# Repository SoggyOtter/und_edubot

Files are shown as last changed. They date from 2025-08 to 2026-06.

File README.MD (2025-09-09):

# UND_EDUBot Overview

[Build Instructions Playlist](https://www.youtube.com/playlist?list=PLYcNE-BB9RCs-w1YGQMMMpfctwIbQ31T8)

# Build the robot

The parts list for the is in the parts list excel file.  Purchase the needed components to build the robot.

If you are building the robot with others several people can build one robot with multi packs of screws and wire.

The CAD models for printing are found in the /build/CAD Models directory.  The .3mf files can be imported directly to the slicer of your choosing for printing.  It is reccommended to use support material, however, acceptable results can be achieved without supports.

Soldering and assembly of the electrical components should be done following the wiring diagram found in the wiring diagram power point in the /build directory

## Tools Needed:

- 3D printer
- Soldering iron & solder
- Metric hex key set
- Small flat head screwdriver
- Small pliers

# Build Instructions

Build instructions will be provided by youtube videos which will be posted.  Following the video instructions and diagrams provide all the information needed to build the robot.

# Powering up for the first time

Once the robot is built you can power up the pi with a flashed micro SD card.

In the /software/Pi Image directory the image for the raspberry pi is provided.  Download the .img file and use the Raspberry Pi Imager to flash the micro SD card with the image.

TODO add images

Select Pi 5 for the pi version

Click on operating system, scroll down and select use custom.  Then find the .img file you downloaded.

Click choose storage and select the micro SD card.  You will be prompted to set the host name and password, choose a name and password you will remember.

# UND Students Pi Image Files

Duplicate the SD card from https://ndusbpos-my.sharepoint.com/:u:/g/personal/john_merila_ndus_edu/EXtqe4LofwhBoTBZhCYkA34BFa9aUKt46IkEdTdlvLatog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 and follow the steps to flash a SD card

I am looking at alternative hosting or compression methods to allow for an image that can be hosted on github.

# Getting the robot running

<!--- The EDUBot uses ROS2 in a Docker container to manage the control of the robot.

Once the pi powers on open VS code, the easiest way is to open a terminal and run

```bash
code .
```

Once in vs code open the PiBot directory using file -> open folder -> PiBot

With the PiBot folder open use the hotkey ctrl+shift+p and type open in container.  This opens the docker container and allows you to control the robot.

BASIC STARTUP
Basic Startup:
 -->
1. 

open terminal and open VS code

```bash
code .
```

2.

file -> open folder

select pibot_repo

click on pop up Reopen in container

if no pop up ctrl-shift-p reopen in container

if it fails ctrl-shift-p rebuild and reopen container

3.

Follow readme located in ws/src/PiBot/Readme.txt

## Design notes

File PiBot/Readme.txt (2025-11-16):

To get RVIZ working
locally: xhost +local:docker

build work space
colcon build --symlink-install
*when first building the workspace it will take some time to build the lidar package
*it will fail on the first build, re run command and it will work

To source the local ROS workspace 
source install/setup.bash

Start up motor control and wheel encoders
ros2 launch PiBot PiBot_launch.py 

Start up lidar with visualization
ros2 launch sllidar_ros2 view_sllidar_a1_launch.py

For teleop control
ros2 run teleop_twist_keyboard teleop_twist_keyboard 

Topics for robot:

/

Notes:

If you are adding additional packages via sudo apt install . . . 

Put at the end of Dockerfile with run preceding
* add -y if it requires yes when installing

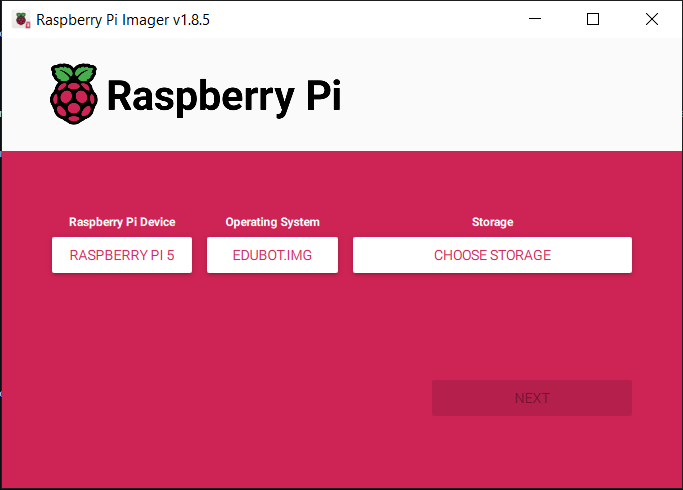
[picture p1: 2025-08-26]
docs/Photos/RPi Imager.PNG

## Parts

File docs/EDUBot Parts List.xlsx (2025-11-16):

Subsystem | Component | Number | Buy No. | Item Cost | Total Cost | Link
Drive | Motors | 2 | 2 | 12.99 | 25.98 | 163 RPM Mini Econ Gear Motor - ServoCity® (https://www.servocity.com/163-rpm-mini-econ-gear-motor/)
 | Wheels | 1 | 1 | 12 | 12 | Pololu Multi-Hub Wheel w/Inserts for 3mm and 4mm Shafts - 80×10mm, Black, 2-Pack (https://www.pololu.com/product/3690)
 | Ball Caster | 1 | 1 | 4.5 | 4.5 | Pololu Ball Caster with 3/4″ Metal Ball (https://www.pololu.com/product/955)
Electronics | Motor Controller | 1 | 1 | 12.99 | 12.99 | Pololu - TB67H420FTG Dual/Single Motor Driver Carrier (https://www.pololu.com/product/2999)
 | Encoders | 2 | 1 | 10 | 10 | Amazon.com: WWZMDiB 4Pcs AS5600 Magnetic Encoder 3.3V 12bit high Precision Magnetic Induction Angle Measurement Sensor Module，Mainly Used to Obtain Information Such as Progressive Motor Speed : Industrial & Scientific (https://www.amazon.com/WWZMDiB-Measurement-Module%EF%BC%8CMainly-Information-Progressive/dp/B0CM3C8KFT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)
 | Rpi | 1 | 1 | 80 | 80 | 2648-SC1112-ND
 | Rpi Active Cooler | 1 | 1 | 5 | 5 | 2648-SC1148-ND
 | Pi Camera | 1 | 1 | 25 | 25 | 2648-SC1223-ND
 | micro HDMI cable | 1 | 1 | 6.99 | 6.99 | Amazon.com: Amazon Basics Micro HDMI to HDMI Display Cable, 18Gbps High-Speed, 4K@60Hz, 2160p, 48-Bit Color, Ethernet Ready, 6 Foot, Black : Electronics (https://www.amazon.com/Amazon-Basics-Display-High-Speed-Ethernet/dp/B07KSDB25X?sp_csd=d2lkZ2V0TmFtZT1zcF9hdGY)
 | Gpio breakout | 1 | 1 | 10.99 | 10.99 | Amazon.com: Treedix RPi GPIO Terminal Block Breakout Board Module Expansion Board Compatible with Raspberry Pi 4B/3B+/3B/2B/Zero/Zero W : Electronics (https://www.amazon.com/Treedix-Terminal-Expansion-Compatible-Raspberry/dp/B09MFB6PJH)
 | Gpio standoff | 1 | 1 | 6.99 | 6.99 | Amazon.com: DSLRKIT 8.5mm GPIO and PoE Pin Header Height Increaser Extender for Raspberry Pi 5 4B 3B+ 3B (Pack of 2) : Electronics (https://www.amazon.com/DSLRKIT-8-5mm-Increaser-Extender-Raspberry/dp/B0F1F84GKV)
 | Lidar | 1 | 1 | 99 | 99 | 1738-1402-ND
 | 3S UPS | 1 | 1 | 32 | 32 | Amazon.com: Waveshare Uninterruptible Power Supply (UPS) Module, Supports Charging and Power Output at The Same Time, 3S & 5V 5A Output, Compatible with Raspberry Pi Board : Electronics (https://www.amazon.com/waveshare-Uninterruptible-UPS-Module-3S/dp/B0BQC2WNR8)
 | Micro USB cable | 1 | 1 | 6.99 | 6.99 | Amazon.com: Short Micro USB Cable 1ft [5 Pack] USB 2.0 Micro USB Charging Cable Android Charger Cord for Samsung Galaxy S7 Edge S6 J7 Note 5 LG Kindle Sony PS4 TV Stick Smartphones (Black) : Electronics (https://www.amazon.com/Android-Compatible-Smartphones-Charging-Stations/dp/B095JZSHXQ)
*6 for price of 3 | 18650 Battery | 3 | 1 | 20 | 20 | Amazon.com: Tokeyla 3.7 Volt 18650 Rechargeable Battery, 3000mAh Battery Flat Top Lithium Batteries for LED Flashlights, Headlamp (6 Pack) : Health & Household (https://www.amazon.com/Tokeyla-Rechargeable-Batteries-Flashlights-Headlamp/dp/B0DRCQHZRH)
 | Micro SD | 1 | 1 | 16.99 | 16.99 | Amazon.com: SanDisk 128GB Extreme microSDXC UHS-I Memory Card with Adapter - Up to 190MB/s, C10, U3, V30, 4K, 5K, A2, Micro SD Card - SDSQXAA-128G-GN6MA : Electronics (https://www.amazon.com/SanDisk-Extreme-microSDXC-Memory-Adapter/dp/B09X7BK27V)
Consumables Note* all of these are more than needed for one robot, if on campus multiple people can share parts | M4x8 | 4 | 1 | 24.98 | 24.98 | HELIFOUNER 1280 Pieces M2 M2.5 M3 M4 304 Stainless Steel Hex Socket Cap Metric Screws Bolts Washers Nuts Hardware Assortment Kit with Hex Wrenches: Amazon.com: Industrial & Scientific (https://www.amazon.com/HELIFOUNER-Stainless-Hardware-Assortment-Wrenches/dp/B09WJ14JWF)
 | M4x12 | 4 |  |  |  | This multi pack is the best way to get all you need for this robot and have extra for other projects
 | M2x8 | 8
 | M2x16 | 2 | Optional
 | M2 Nuts | 2 | Optional
 | M2.5x8 | 8
 | 24 gauge wire multi color |  | 1 | 15.99 | 15.99 | TUOFENG 24 AWG Flexible Silicone Wire, 30ft/9m Each (6 Colors), Tinned Copper Core, High Temp Resistant (-60C to +200C), Suitable for Electrical & Electronic Devices - Amazon.com (https://www.amazon.com/TUOFENG-Wire-Stranded-Flexible-Silicone-Different/dp/B07G2BWBX8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)
 | 20 gauge wire red/black |  | 1 | 10.98 | 10.98 | https://www.amazon.com/BNTECHGO-Silicone-Flexible-Strands-Stranded/dp/B07HGT7N29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
 | PLA Filament | 1
 | Small Zipties |  | 1 | 2.99 | 2.99 | Amazon.com: Zip Ties 4 inch, Small Zip Ties with 18 lb Tensile Strength, Black, 1000 Pack, by Tantti Supply : Electronics (https://www.amazon.com/Small-Tensile-Strength-Tantti-Supply/dp/B0C2KGK2HR?sp_csd=d2lkZ2V0TmFtZT1zcF9hdGY)
Optional Accessories | Small Router | 1 | 1 | 34 | 34 | Amazon.com: GL.iNet GL-AR300M16-Ext Portable Mini Travel Wireless Pocket Router - WiFi Router | OpenWrt | 2 x Ethernet Ports | OpenVPN/Wireguard VPN for Public & Hotel Wi-Fi | USB 2.0 Port | 2 x External Antennas : Electronics (https://www.amazon.com/GL-iNet-GL-AR300M16-Ext-Pre-Installed-Performance-Programmable/dp/B07794JRC5)
 |  |  |  | Total Cost | 464.36
 |  |  |  | w/o consumables | 409.42

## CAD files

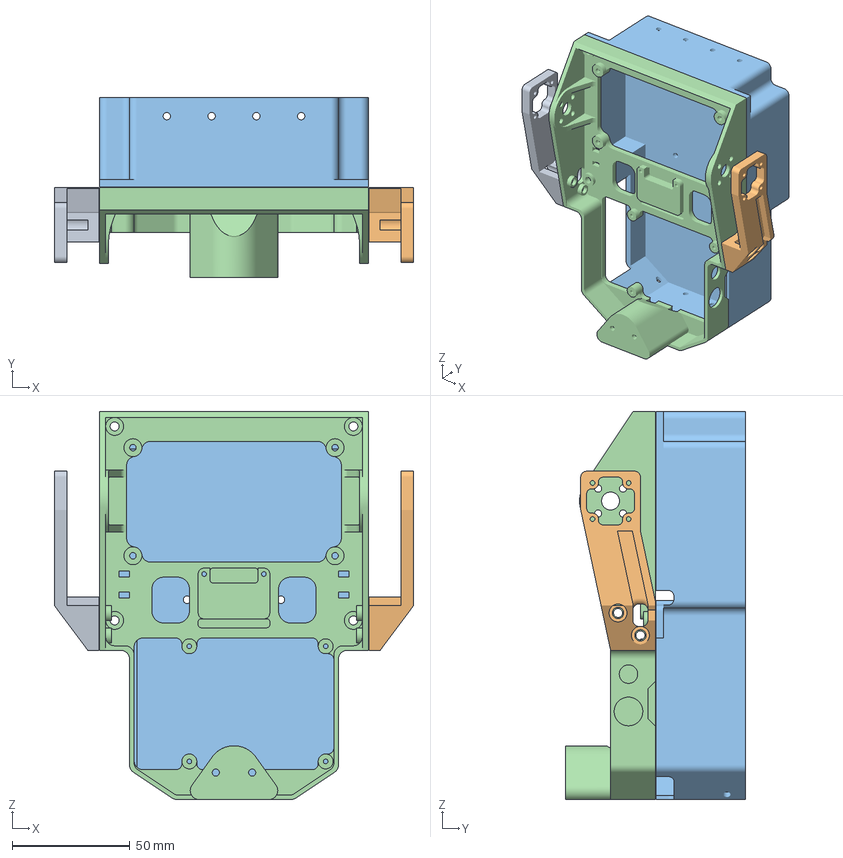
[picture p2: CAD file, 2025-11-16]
docs/Build/CAD Models/body_platev2v2.3mf
152.9 x 76.6 x 165.1 mm
BODY_PLATEV2_0_body_0
BODY_PLATEV2_0_body_1
BODY_PLATEV2_0_body_2
BODY_PLATEV2_1

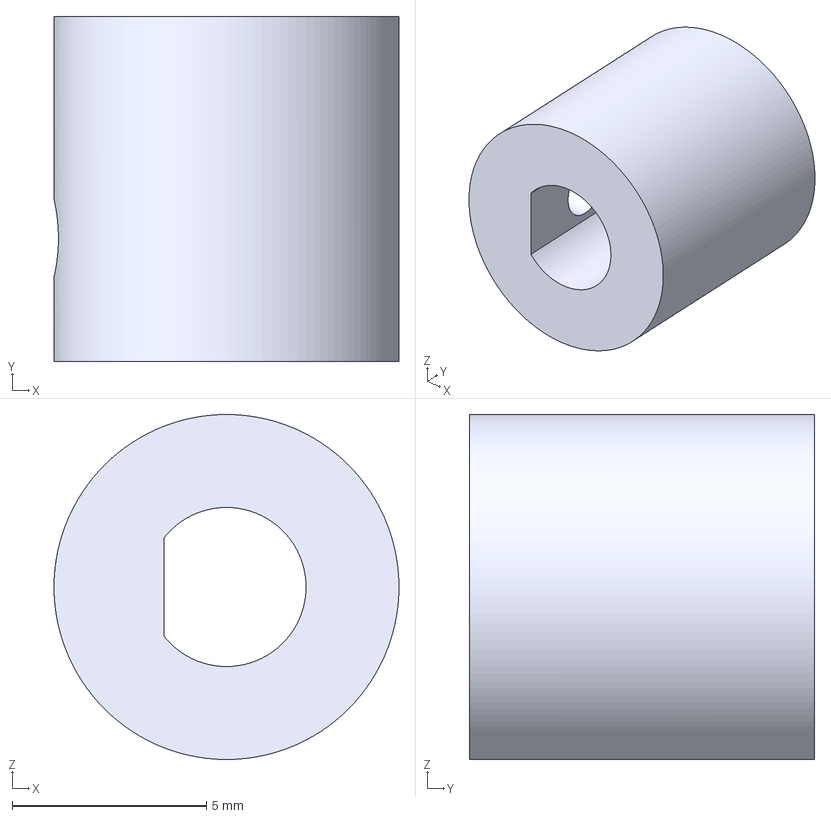
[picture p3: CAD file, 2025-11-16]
docs/Build/CAD Models/encoder_adapter.3mf
8.89 x 8.89 x 8.89 mm

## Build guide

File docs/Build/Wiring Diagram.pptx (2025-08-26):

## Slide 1

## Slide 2

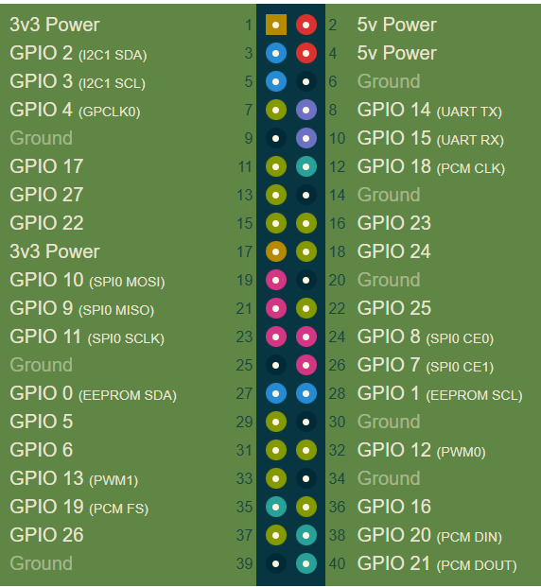
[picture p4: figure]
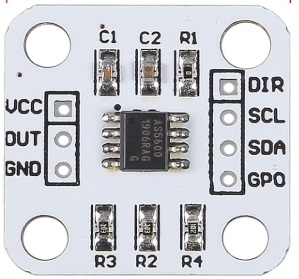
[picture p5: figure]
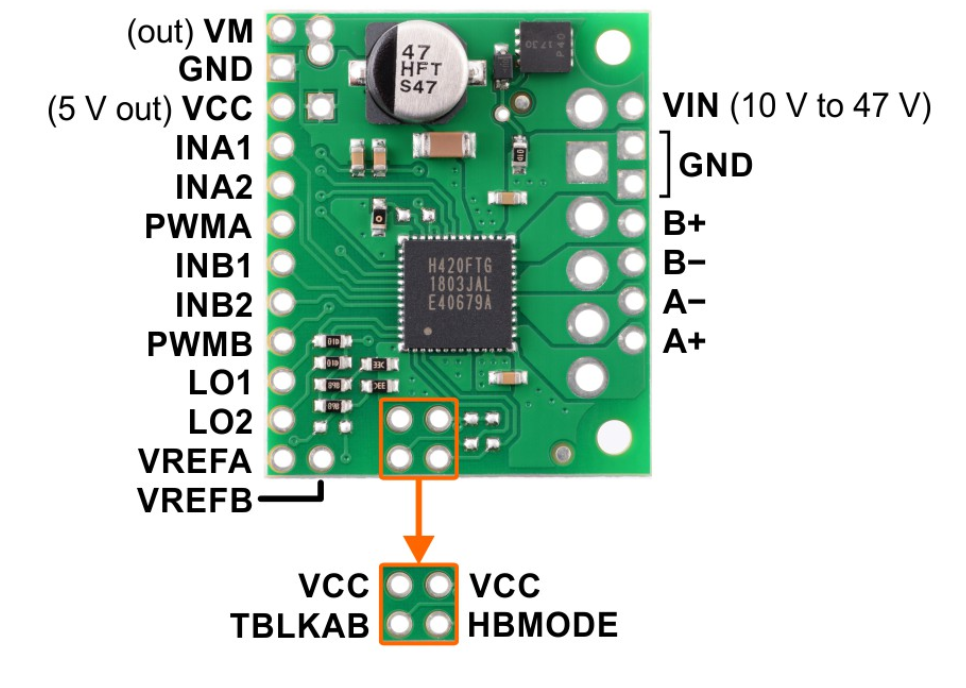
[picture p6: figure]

Pi pin
INA1 -> 22
INA2 -> 12
INB1 -> 8
INB2 -> 10
LSCL -> 5
LSDA -> 3
RSCL -> 21
RSDA -> 24

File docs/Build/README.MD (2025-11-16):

Purchase components in the parts list

if you are building the robot on your own the consumables may already be in your parts inventory or purchasing the bulk packs adds more parts to your inventory

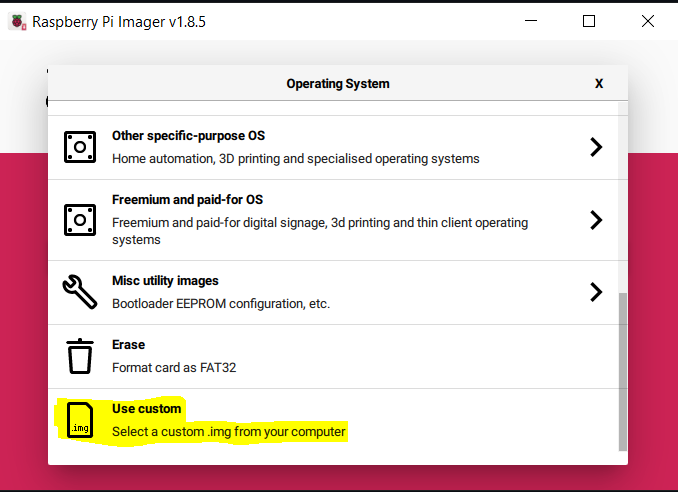
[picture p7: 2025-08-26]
docs/Photos/Operating System Selection.PNG

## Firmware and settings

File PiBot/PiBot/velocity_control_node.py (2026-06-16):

import rclpy
from rclpy.node import Node
from rclpy.callback_groups import MutuallyExclusiveCallbackGroup

from geometry_msgs.msg import Twist
from std_msgs.msg import Float64
from sensor_msgs.msg import JointState
from gpiozero import Motor


MAX_RPM = 163.0
MAX_RPS = MAX_RPM / 60.0


class VelocityController(Node):
    def __init__(self):
        super().__init__("velocity_controller")

        # Subscriptions
        self.create_subscription(Twist, "/cmd_vel", self.set_motor_speed, 10)
        self.create_subscription(
            JointState,
            "/joint_states",
            self.calculate_error,
            10,
            callback_group=MutuallyExclusiveCallbackGroup(),
        )

        # Publishers
        self.motor_1_err_pub = self.create_publisher(Float64, "motor_1/velocity_error", 10)
        self.motor_2_err_pub = self.create_publisher(Float64, "motor_2/velocity_error", 10)

        # Motors
        self.motor_1 = Motor(25, 18)
        self.motor_2 = Motor(14, 15)

        # Targets
        self.m1vel_target = 0.0
        self.m2vel_target = 0.0

        # PID state
        self.m1_err_int = 0.0
        self.m2_err_int = 0.0
        self.m1_prev_vel = 0.0
        self.m2_prev_vel = 0.0

        self.dvel1_filt = 0.0
        self.dvel2_filt = 0.0

        self.m1vel_pwm = 0.0
        self.m2vel_pwm = 0.0
        self.m1vel_pwm_prev = 0.0
        self.m2vel_pwm_prev = 0.0

        # Timing
        self.last_pid_time = self.get_clock().now()

        # Smoothing
        self.max_pwm_rate = 2.0     # PWM units per second
        self.d_alpha = 0.2          # derivative low-pass
        self.deadband = 0.03

        self.declare_params()

        # Motor update timer
        self.create_timer(1.0 / 20.0, self.do_drive_motor)

    # -----------------------------------------------------

    def declare_params(self):
        self.declare_parameter("motor1.kp", 0.37)
        self.declare_parameter("motor1.ki", 0.15)
        self.declare_parameter("motor1.kd", 0.005)

        self.declare_parameter("motor2.kp", 0.35)
        self.declare_parameter("motor2.ki", 0.15)
        self.declare_parameter("motor2.kd", 0.005)

    # -----------------------------------------------------

    def set_motor_speed(self, msg: Twist):
        self.m1vel_target = msg.linear.x
        self.m2vel_target = msg.linear.x
        
        if msg.angular.z != 0:
            self.m1vel_target = -msg.angular.z
            self.m2vel_target = msg.angular.z

    # -----------------------------------------------------

    def rate_limit(self, desired, current, dt):
        max_delta = self.max_pwm_rate * dt
        return max(current - max_delta, min(current + max_delta, desired))

    def apply_deadband(self, u):
        if abs(u) < self.deadband:
            return 0.0
        return u

    # -----------------------------------------------------

    def calculate_error(self, msg: JointState):
        now = self.get_clock().now()
        dt = (now - self.last_pid_time).nanoseconds * 1e-9
        self.last_pid_time = now
        if dt <= 0.0:
            return

        vel_L_rps = msg.velocity[0] / 360.0
        vel_R_rps = msg.velocity[1] / 360.0

        err1 = self.m1vel_target - vel_L_rps
        err2 = self.m2vel_target - vel_R_rps

        self.motor_1_err_pub.publish(Float64(data=err1))
        self.motor_2_err_pub.publish(Float64(data=err2))

        # Integral
        self.m1_err_int += err1 * dt
        self.m2_err_int += err2 * dt
        self.m1_err_int = max(-1.0, min(1.0, self.m1_err_int))
        self.m2_err_int = max(-1.0, min(1.0, self.m2_err_int))

        # Derivative (filtered, on measurement)
        raw_d1 = (vel_L_rps - self.m1_prev_vel) / dt
        raw_d2 = (vel_R_rps - self.m2_prev_vel) / dt
        self.m1_prev_vel = vel_L_rps
        self.m2_prev_vel = vel_R_rps

        self.dvel1_filt += self.d_alpha * (raw_d1 - self.dvel1_filt)
        self.dvel2_filt += self.d_alpha * (raw_d2 - self.dvel2_filt)

        # Gains
        kp1 = self.get_parameter("motor1.kp").value
        ki1 = self.get_parameter("motor1.ki").value
        kd1 = self.get_parameter("motor1.kd").value

        kp2 = self.get_parameter("motor2.kp").value
        ki2 = self.get_parameter("motor2.ki").value
        kd2 = self.get_parameter("motor2.kd").value

        # PID output
        pid1 = kp1 * err1 + ki1 * self.m1_err_int - kd1 * self.dvel1_filt
        pid2 = kp2 * err2 + ki2 * self.m2_err_int - kd2 * self.dvel2_filt

        # Rate limit
        pid1 = self.rate_limit(pid1, self.m1vel_pwm_prev, dt)
        pid2 = self.rate_limit(pid2, self.m2vel_pwm_prev, dt)

        # Deadband
        self.m1vel_pwm = self.apply_deadband(pid1)
        self.m2vel_pwm = self.apply_deadband(pid2)

        # Clamp
        self.m1vel_pwm = max(-1.0, min(1.0, self.m1vel_pwm))
        self.m2vel_pwm = max(-1.0, min(1.0, self.m2vel_pwm))

        self.m1vel_pwm_prev = self.m1vel_pwm
        self.m2vel_pwm_prev = self.m2vel_pwm

    # -----------------------------------------------------

    def do_drive_motor(self):
        if self.m1vel_pwm >= 0:
            self.motor_1.forward(abs(self.m1vel_pwm))
        else:
            self.motor_1.backward(abs(self.m1vel_pwm))

        if self.m2vel_pwm >= 0:
            self.motor_2.forward(abs(self.m2vel_pwm))
        else:
            self.motor_2.backward(abs(self.m2vel_pwm))


def main(args=None):
    rclpy.init(args=args)
    node = VelocityController()
    rclpy.spin(node)
    rclpy.shutdown()


if __name__ == "__main__":
    main()

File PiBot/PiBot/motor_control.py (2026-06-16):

import rclpy
from rclpy.node import Node

from geometry_msgs.msg import Twist
from gpiozero import Motor
from time import sleep

class MinimalSubscriber(Node):
	
	def __init__(self):
		super().__init__('node')
		self.subscription = self.create_subscription(
			Twist,
			'/cmd_vel',
			self.listener_callback,
			10)
		self.subscription  # prevent unused variable warning
		self.m1vel = None
		self.m2vel = None
	def listener_callback(self, msg):
		
		self.get_logger().info('I heard: "%s"' % msg.linear)
		linearvel = msg.linear.x
		angularvel = msg.angular.z
  
		if linearvel != 0 and angularvel != 0:
      
			m1vel_temp = linearvel*.8 + angularvel*.25
			m2vel_temp = linearvel*.8 - angularvel*.25
			if m1vel_temp > 1:
				m1vel_temp = 1
			elif m1vel_temp < -1:
				m1vel_temp = -1
			if m2vel_temp > 1:
				m2vel_temp = 1
			elif m2vel_temp < -1:
				m2vel_temp = -1
    
		else:
		
			m1vel_temp = linearvel*.8 + angularvel*.25
			m2vel_temp = linearvel*.8 - angularvel*.25
			if m1vel_temp > 1:
				m1vel_temp = 1
			elif m1vel_temp < -1:
				m1vel_temp = -1
			if m2vel_temp > 1:
				m2vel_temp = 1
			elif m2vel_temp < -1:
				m2vel_temp = -1
		self.get_logger().info('I heard: "%s"' % m1vel_temp)
		self.get_logger().info('I heard: "%s"' % m2vel_temp)
	
		self.m1vel = m1vel_temp*.8
		self.m2vel = m2vel_temp*.8
		
		


def main(args=None):
	rclpy.init(args=args)
	motor1 = Motor(25,18)
	motor2 = Motor(14,15)

	
	node = MinimalSubscriber()

	try:
		while rclpy.ok():
			rclpy.spin_once(node, timeout_sec=0.1)
			if node.m1vel and node.m2vel:
				# Use the stored value here

				print(node.m1vel)
				print(node.m2vel)
				# if node.m1vel > 0:
				# 	motor1.forward(node.m1vel)
				# else:
				# 	motor1.backward(abs(node.m1vel))
				if node.m2vel > 0:
					motor2.forward(node.m2vel)
				else:
					
					motor2.backward(abs(node.m2vel))
			else:
				motor1.forward(0)
				motor2.forward(0)
				#print(f"[Main loop] linear.x = {node.m1vel})
	except KeyboardInterrupt:
		motor1.forward(0)
		motor2.forward(0)
		pass
	node.destroy_node()
	rclpy.shutdown()


if __name__ == '__main__':
	main()

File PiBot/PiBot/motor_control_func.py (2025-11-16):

import RPi.GPIO as GPIO
import os
#import time
#import math
print(GPIO.RPI_INFO)
# Set up GPIO mode
for dev in ['/dev/gpiomem', '/dev/gpiomem0', '/dev/mem']:
    print(f"{dev}: {'exists' if os.path.exists(dev) else 'missing'}")
#GPIO.setmode(GPIO.BOARD)

GPIO.RPI_INFO['P1_REVISION'] = 3  # or 2 or 1 depending on your Pi
GPIO.setmode(GPIO.BCM)
# Motor 1 Pins

#EN1_PIN = 25  # Use a PWM pin
M1_PWM1_PIN = 12   
M1_PWM2_PIN = 22

M2_PWM1_PIN = 8   
M2_PWM2_PIN = 10

#EN1_PIN = 22  # Use a PWM pin
#PWM1_PIN = 18   
#PWM2_PIN = 25

# Setup GPIO pins
GPIO.setup(M1_PWM1_PIN, GPIO.OUT)
GPIO.setup(M1_PWM2_PIN, GPIO.OUT)

GPIO.setup(M2_PWM1_PIN, GPIO.OUT)
GPIO.setup(M2_PWM2_PIN, GPIO.OUT)

# Set up PWM on the pins with a frequency of 1000Hz
pwm1_motor1 = GPIO.PWM(M1_PWM1_PIN, 1000)
pwm2_motor1 = GPIO.PWM(M1_PWM2_PIN, 1000)

pwm1_motor2 = GPIO.PWM(M2_PWM1_PIN, 1000)
pwm2_motor2 = GPIO.PWM(M2_PWM2_PIN, 1000)

# Start PWM with 0 duty cycle (motors stopped)
pwm1_motor1.start(0)
pwm2_motor1.start(0)

pwm1_motor2.start(0)
pwm2_motor2.start(0)

# Function to control motor direction and speed
def control_motor(motor_num, speed):
    if motor_num == 1:
        if speed > 0:
            print("FORWARD")
            pwm1_motor1.ChangeDutyCycle(abs(speed))       # Speed is between 0-100%
            pwm2_motor1.ChangeDutyCycle(0)       # Speed is between 0-100%

        elif speed < 0:
            print("Reverse")
            pwm1_motor1.ChangeDutyCycle(0)       # Speed is between 0-100%
            pwm2_motor1.ChangeDutyCycle(abs(speed))       # Speed is between 0-100%
            print("FORWARD")
        else:
            pwm1_motor1.ChangeDutyCycle(0)       # Speed is between 0-100%
            pwm2_motor1.ChangeDutyCycle(0)       # Speed is between 0-100%

    if motor_num == 2:
        if speed < 0:
            print("FORWARD")
            pwm1_motor2.ChangeDutyCycle(abs(speed))       # Speed is between 0-100%
            pwm2_motor2.ChangeDutyCycle(0)       # Speed is between 0-100%

        elif speed > 0:
            print("Reverse")
            pwm1_motor2.ChangeDutyCycle(0)       # Speed is between 0-100%
            pwm2_motor2.ChangeDutyCycle(abs(speed))       # Speed is between 0-100%
            print("FORWARD")
        else:
            pwm1_motor2.ChangeDutyCycle(0)       # Speed is between 0-100%
            pwm2_motor2.ChangeDutyCycle(0)       # Speed is between 0-100%

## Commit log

2025-08-26 Wiring Diagram
2025-11-16 Update project structure to be more conducive to typically dev workflow
    [EDUBot Parts List.xlsx, body_platev2v2.3mf, encoder_adapter.3mf]
2025-12-13 add vibe coded pid
